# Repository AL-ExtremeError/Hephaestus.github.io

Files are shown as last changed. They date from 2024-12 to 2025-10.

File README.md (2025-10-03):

# Hephaestus.github.io

Welcome to the Hephaestus Build Guide!

<p align="center">
<a href="https://youtube.com/shorts/SWLXf19VgqY?feature=share" target="_blank">
  Youtube Video
</a>
</p>

****

For the updated **"Medusa"** build, please click here for that repository: https://github.com/AL-ExtremeError/Medusa

****

This guide will provide information, walk-thru's and files for a CoreXY Conversion of an Elegoo Neptune 4 Max 3d Printer in which I call, Hephaestus (heh-FESS-tus).

**Please Note:** Under the Build Documentation section, the links are listed in the order in which this build was done.

**Disclaimer:** This build is a DIY and at your own risk. There is no affiliation with Elegoo, Partners or vendors. I am not being compensated in my way for this. This walk-thru is strictly based on my own experience of my own personal challenge. I am not responsible for any mistakes, mis-interpretations and /or but not limited to mis-understandings. If something in this walk-thru is not clear or you would like to provide feedback (Good, Bad or Indifferent), please feel free reach out. I welcome all feedback and I am more than happy to answer / help walk-thru as best as I can.

**General Information**
* [Materials & Cost](https://github.com/AL-ExtremeError/Hephaestus.github.io/wiki/Hephaestus-Materials-&-Cost)
* [Design & Dimensions](https://github.com/AL-ExtremeError/Hephaestus.github.io/wiki/Hephaestus-Design-&-Dimensions)
* [Links](https://github.com/AL-ExtremeError/Hephaestus.github.io/wiki/Links)
* [Video Links](https://github.com/AL-ExtremeError/Hephaestus.github.io/wiki/Video-Links)

**Build Documentation**
* [Software Build](https://github.com/AL-ExtremeError/Hephaestus.github.io/wiki/Hephaestus-Build)
* [Cage Build](https://github.com/AL-ExtremeError/Hephaestus.github.io/wiki/Cage-Build)
* [Additional-Supports-&-Z-Axis-Build-Plate-Support](https://github.com/AL-ExtremeError/Hephaestus.github.io/wiki/Additional-Supports-&-Z-Axis-Build-Plate-Support)
* [Z-Axis Linear-Rails,-Stepper-Motors-&-Lead-Screws](https://github.com/AL-ExtremeError/Hephaestus.github.io/wiki/Z%E2%80%90Axis-%E2%80%90-Linear-Rails,-Stepper-Motors-&-Lead-Screws)
* [Bed Plate Build](https://github.com/AL-ExtremeError/Hephaestus.github.io/wiki/Bed-Plate-Build)
* [Y-Axis Build](https://github.com/AL-ExtremeError/Hephaestus.github.io/wiki/Y%E2%80%90Axis-Build)
* [X-Axis Build](https://github.com/AL-ExtremeError/Hephaestus.github.io/wiki/X%E2%80%90Axis-Build)
* [Stepper Motors, Belts & Tensioning](https://github.com/AL-ExtremeError/Hephaestus.github.io/wiki/Stepper-Motors,-Belts-&-Tensioning)
* [Print-Head-Tool-Mount](https://github.com/AL-ExtremeError/Hephaestus.github.io/wiki/Print-Head-%E2%80%90-Tool-Mount)
* [Board Box, Wiring & Electrical](https://github.com/AL-ExtremeError/Hephaestus.github.io/wiki/Board-Box,-Wiring-&-Electrical)
* [LED Light Bar](https://github.com/AL-ExtremeError/Hephaestus.github.io/wiki/LED-Light-Bar)

***

* **[Links](https://github.com/AL-ExtremeError/Hephaestus.github.io/wiki/Links)**

<p align="center">
<a href="https://ko-fi.com/alextremeerror" target="_blank">
  
</a>
</p>

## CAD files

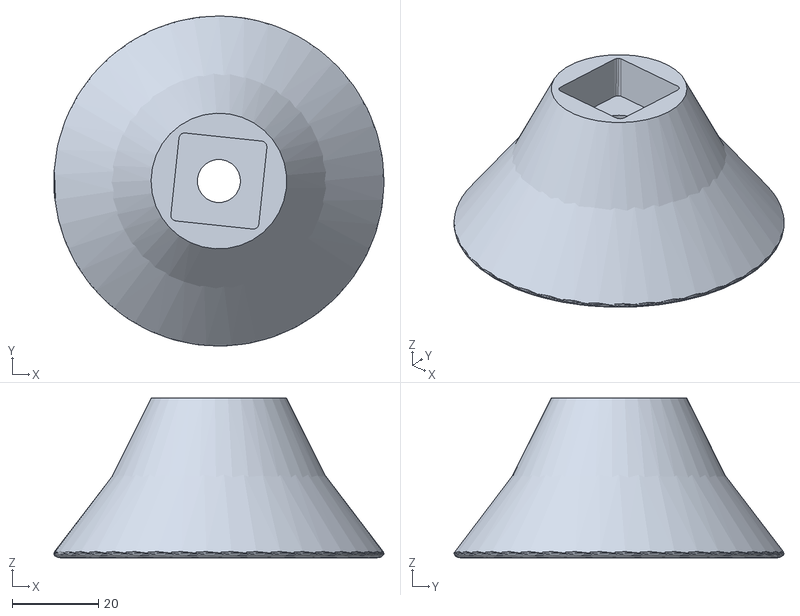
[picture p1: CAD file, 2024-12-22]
STL Files/Misc_Parts/Elegoo_Printer_Corner_Base_Feet.stl
76.5 x 76.5 x 37.0

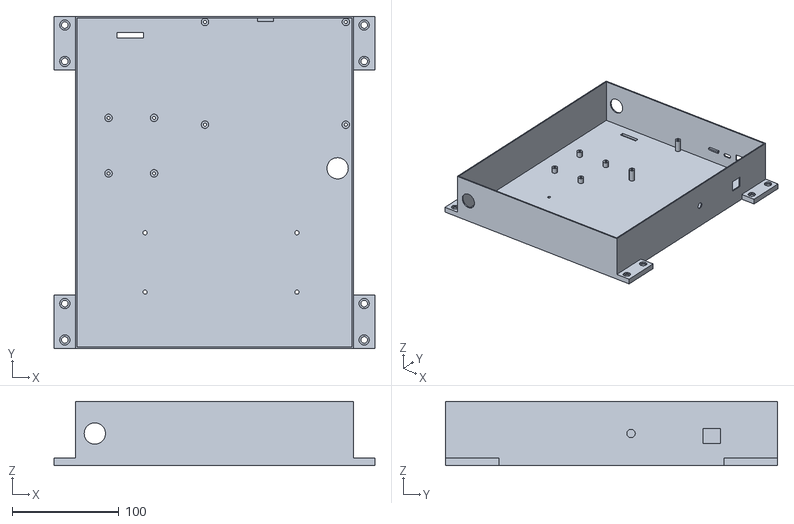
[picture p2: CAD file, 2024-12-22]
STL Files/PowerSupply and Board/Power_Supply_And_Board_Box.stl
300.0 x 310.5 x 60.0

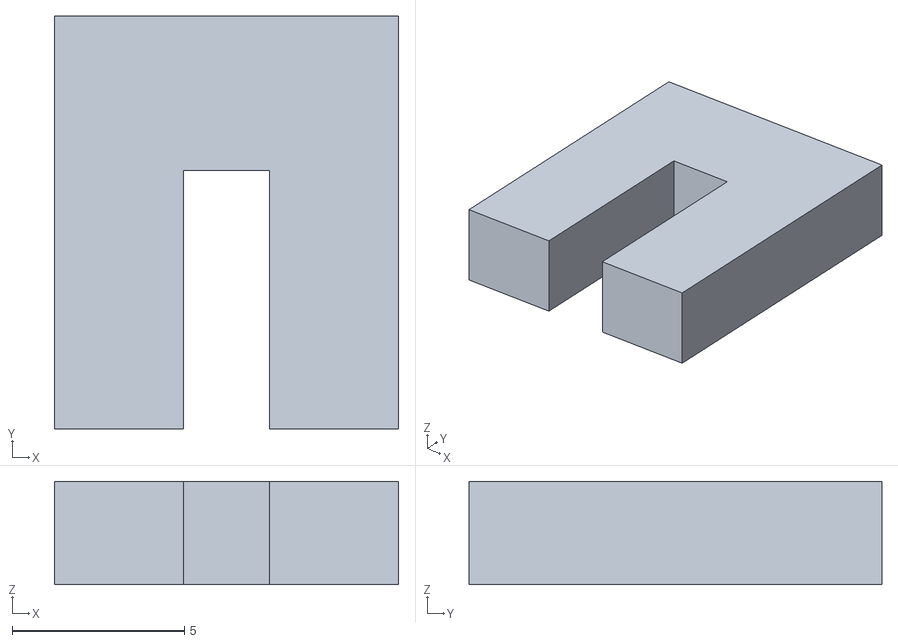
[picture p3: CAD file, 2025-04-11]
STL Files/X Axis Tool Head Carriage/X_Carriage_Belt_Clip_Shim.stl
10.0 x 12.0 x 3.00

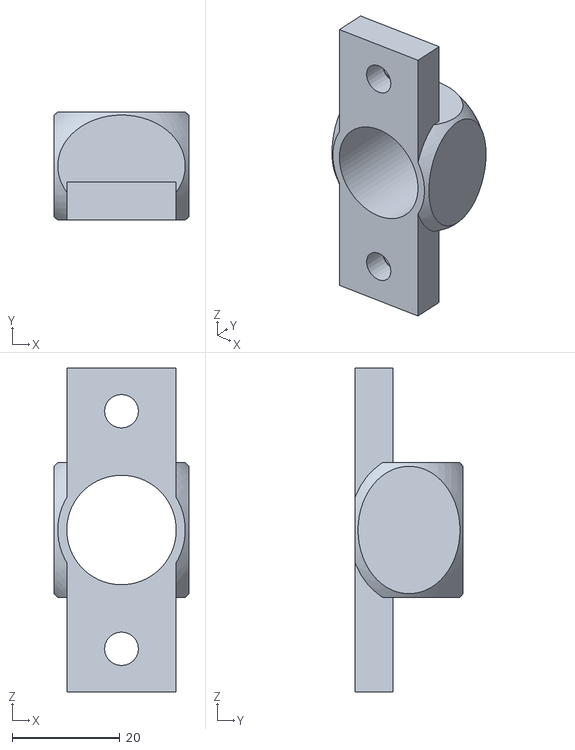
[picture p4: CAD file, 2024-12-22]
STL Files/Y Axis/Y_Axis_Rod_Holder_Front_V2_11.2.2024.stl
25.0 x 20.0 x 60.0

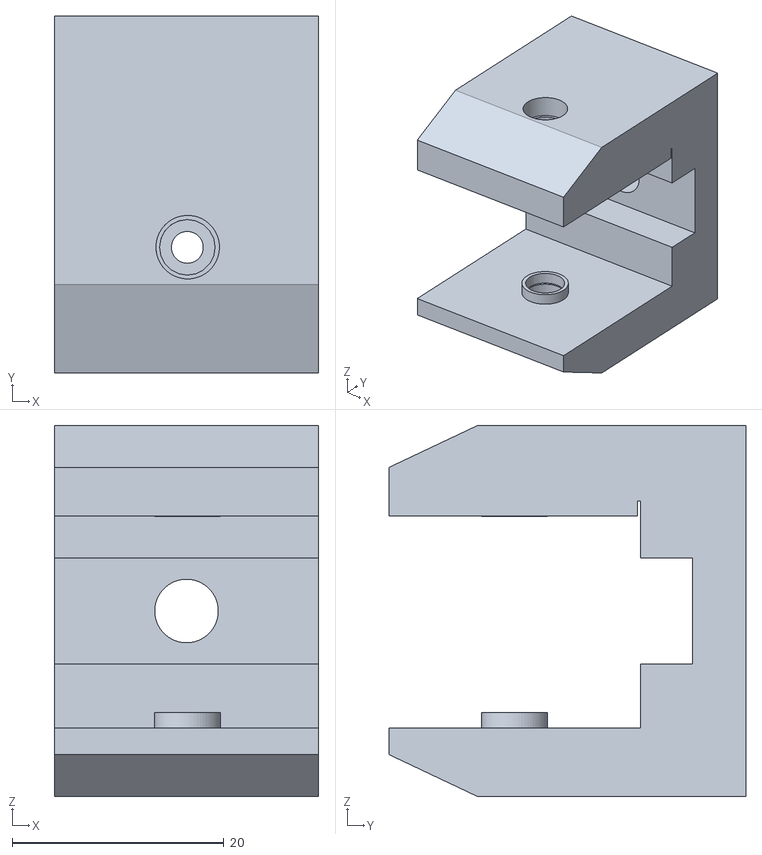
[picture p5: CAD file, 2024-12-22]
STL Files/Y Axis/Y_Pulley_Wheel_Holder/Y_Pulley_Wheel_Holder.stl
25.0 x 33.7 x 35.1

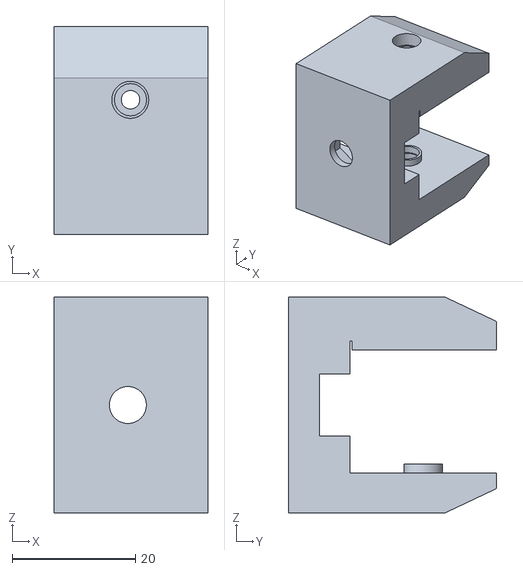
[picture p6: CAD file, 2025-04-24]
STL Files/Y Axis/Y_Pulley_Wheel_Holder_Alternate/Y_Pulley_Wheel_Holder_Alt.stl
25.0 x 33.7 x 35.1

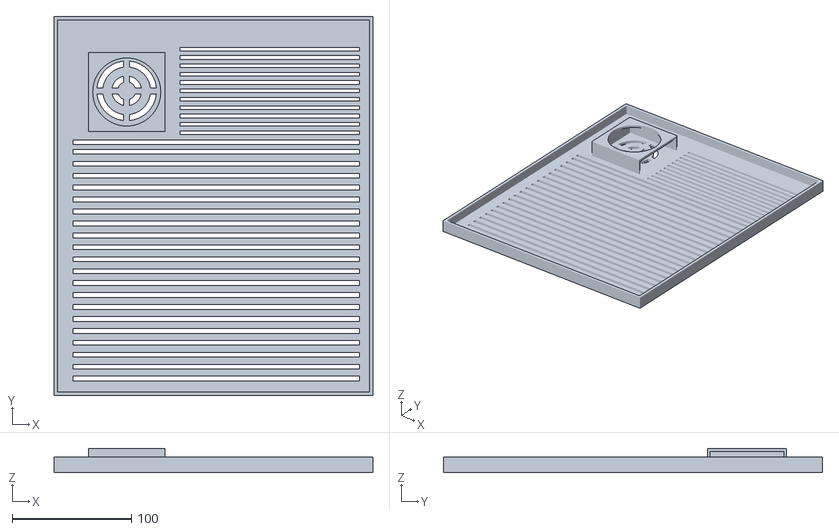
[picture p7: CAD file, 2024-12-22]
STL Files/PowerSupply and Board/Power_Supply_And_Board_Box_Cover.stl
267.0 x 317.5 x 20.3

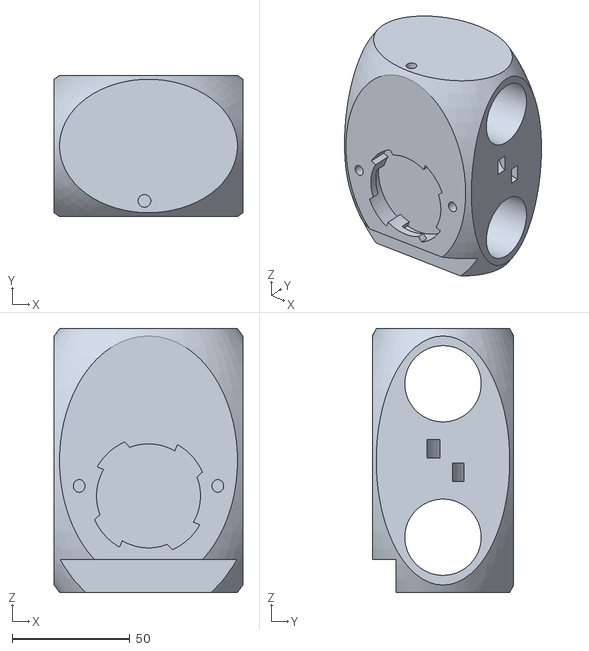
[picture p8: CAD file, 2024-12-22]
STL Files/X Axis Tool Head Carriage/X_Axis_Carriage_Tool_Carriage_V2_11.13.2024.stl
80.0 x 60.0 x 112.0

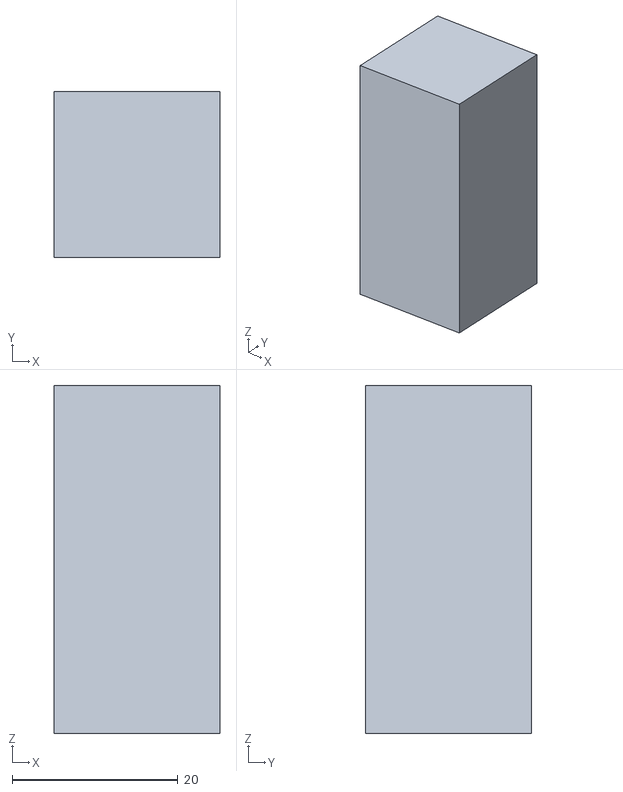
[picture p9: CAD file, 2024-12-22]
STL Files/Y Axis/Y_Axis_Rod_Setting_Bar.2024.stl
20.0 x 20.0 x 42.0

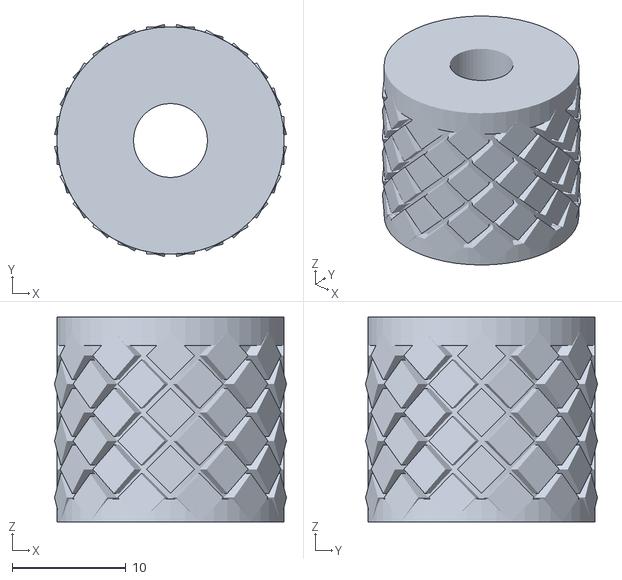
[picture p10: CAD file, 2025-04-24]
STL Files/Y Axis/Y_Pulley_Wheel_Holder_Alternate/Y_Pulley_Wheel_Holder_Alt_Knob.stl
20.4 x 20.4 x 18.0

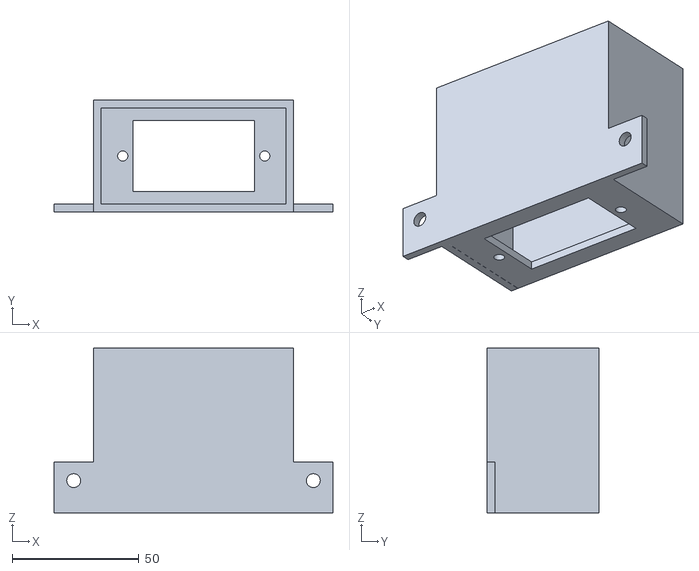
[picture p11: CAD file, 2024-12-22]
STL Files/PowerSupply and Board/Power_Supply_Switch_Box.stl
110.0 x 44.0 x 65.0

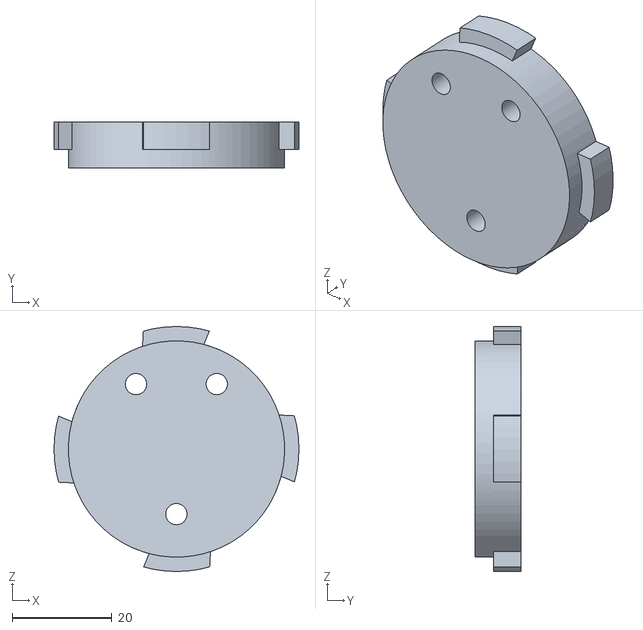
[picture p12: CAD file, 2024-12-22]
STL Files/X Axis Tool Head Carriage/X_Axis_Carriage_Tool_Mount_V2_11.3.2024.stl
49.0 x 9.25 x 49.0

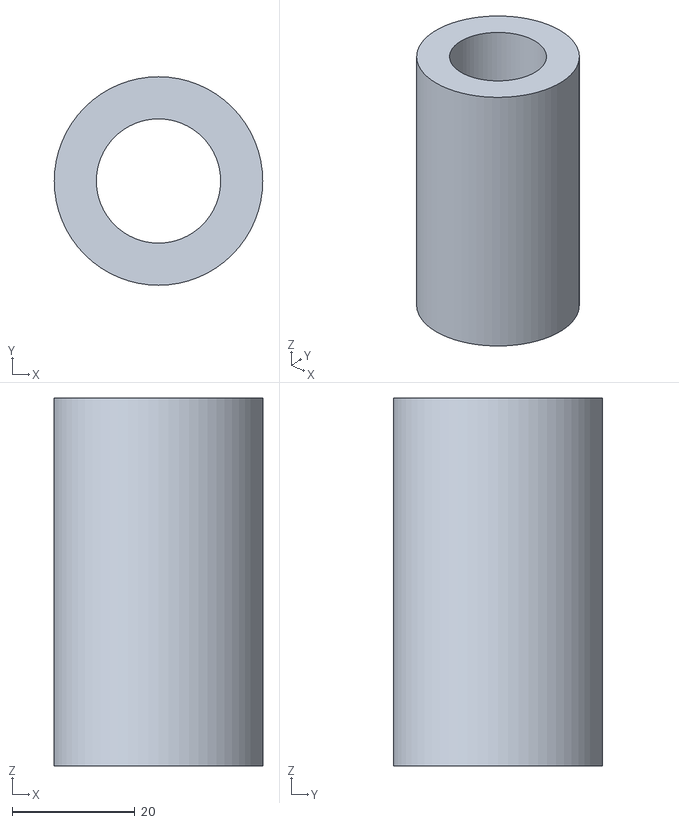
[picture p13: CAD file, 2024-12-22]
STL Files/Y Axis/End_Stops_Front_11.13.2024.stl
34.0 x 34.0 x 60.0

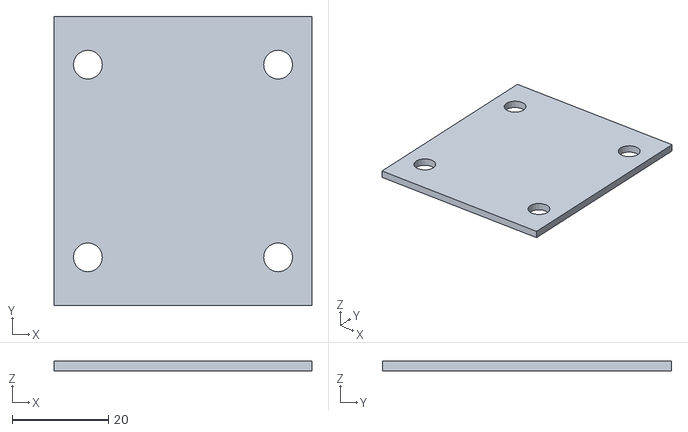
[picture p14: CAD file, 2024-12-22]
STL Files/Z Axis/Z Axis_Carriage_Shim.stl
53.5 x 60.0 x 2.00

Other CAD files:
STL Files/Y Axis/Y_Axis_Carriage_V3_11.24.2024.stl
STL Files/Y Axis/Y_Pulley_Tensioner_Rear_Right.stl
STL Files/Y Axis/Y_Axis_Rod_Holder_Rear_Left_V3_11.13.2024.stl
STL Files/Z Axis/Z_Axis_Nut_Block.stl
STL Files/Z Axis/Z_Axis_Nut_Block_Spacer.stl

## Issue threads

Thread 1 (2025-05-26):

Firmware version for two Z motors from one driver

DBSDBS, 2025-05-26:
Hello,

Is there a version for the firmware that uses the original configuration with single driver for the two Z motors?

Thank you in advance.

Denis

AL-ExtremeError, 2025-05-26:
If you mean to control the two motors individually, no. Not that I am aware of anyway.

The driver supports one channel for lack of a better term. So whatever signal is sent from that "channel" is what will be received by whatever is connected to it.

If you want to control each motor individually, then each one will need a driver independently.

Now if you jist want to connect two Z motors to have them driven by one driver, the neptune 4 max is already setup that way from stock as it uses a splitter cable to connect both stepper motors to one driver. Unfortunately, this means that that is no independency but will suffice to get z moving with 2 motors.

I hope this helps

DBSDBS, 2025-05-26:
Thank you for the replay...
Because you share a CoreXY firmware that is modified also for two drivers (Z and E1) to drive separately the two Z motors (in yours case), I asked for the same firmware made from you for CoreXY but without Z section modifications - only original one driver for Z.

DBSDBS, 2025-05-27:
I'm using opennep4tune firmware. What should I to exchange in it to be able to use your version of CoreXY N4M?

AL-ExtremeError, 2025-06-06:
I am so sorry, I never got an alert that you had replied. The default items within the printer.cfg file that come with opennep4tune should work fine as I was using the default when I did it. The only thing is you will need to make sure your gpio's are configured correctly and small details like that but over all it should all work with default.

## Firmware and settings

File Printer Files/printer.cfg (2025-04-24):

#----------------------------------------------------------------------------
#      ____                _  __         __  ____              
#     / __ \___  ___ ___  / |/ /__ ___  / /_/ / /__ _____  ___ 
#    / /_/ / _ \/ -_) _ \/    / -_) _ \/ __/_  _/ // / _ \/ -_)
#    \____/ .__/\__/_//_/_/|_/\__/ .__/\__/ /_/ \_,_/_//_/\__/ 
#        /_/                    /_/                            
#----------------------------------------------------------------------------
;   Neptune 4 Series Custom Image by (OpenNeptune3D/OpenNept4une):
#----------------------------------------------------------------------------
; Wiki    : https://github.com/OpenNeptune3D/OpenNept4une/wiki
; Discord : https://discord.com/invite/X6kwchT6WM

#############################################################################
#   External Config Includes
#############################################################################
[include mainsail.cfg]          ; mainsail runs on port 81 (http://IP_ADDRESS:81)
[include fluidd.cfg]
[include KAMP_Settings.cfg]
[include Adaptive_Meshing.cfg] 
[include Smart_Park.cfg]
[include Line_Purge.cfg]
#[include shell_command.cfg]
#[include klipper_debug.cfg]
#[include adxl.cfg]             ; Comment this out when you disconnect the Pico/MellowFly
#[include timelapse.cfg]


#############################################################################
#   Base Config
#############################################################################

[virtual_sdcard]
path: ~/printer_data/gcodes
[display_status]
[pause_resume]

[mcu]
serial: /dev/ttyS0 ; The hardware use USART1 PA10/PA9 connect to RK3328
baud: 250000
restart_method: command

[printer]
kinematics: corexy
max_velocity: 500
max_accel: 10000
max_z_velocity: 8
max_z_accel: 120
square_corner_velocity: 9.0
minimum_cruise_ratio: 0.1

[respond]
[gcode_arcs]
[pause_resume]
[display_status]
[exclude_object]
[firmware_retraction]
[virtual_sdcard]
path: ~/printer_data/gcodes
[force_move]
enable_force_move : True
[idle_timeout]
timeout: 2100                  ; 35min idle timeout (when not paused or printing)

#############################################################################
#   X/Y/Z Stepper Config
#############################################################################

[stepper_x]
step_pin: PC14
dir_pin: PC13
enable_pin: !PC15
microsteps: 64
rotation_distance: 40
full_steps_per_rotation:200                  ; set to 400 for 0.9 degree stepper
endstop_pin: tmc2209_stepper_x:virtual_endstop
position_min: 0
position_max: 415
position_endstop: 415
homing_speed: 40
homing_retract_dist: 0
homing_positive_dir: True

[stepper_y]
step_pin: PB4
dir_pin: !PB3
enable_pin: !PC15
microsteps: 64
rotation_distance: 40
full_steps_per_rotation:200                  ; set to 400 for 0.9 degree stepper
endstop_pin: tmc2209_stepper_y:virtual_endstop
position_min: 0
position_max: 415
position_endstop: 415
homing_speed:40
homing_retract_dist: 0
homing_positive_dir: True

[stepper_z]
step_pin: PC10
dir_pin: PA13
enable_pin: !PC11
microsteps: 32
rotation_distance: 2
full_steps_per_rotation: 200
endstop_pin:probe:z_virtual_endstop
position_min: -1
position_max: 700
homing_speed: 8
second_homing_speed: 3
homing_retract_dist: 5
homing_positive_dir: False


[stepper_z1]
step_pin: PB1
dir_pin: !PB2
enable_pin: !PB0
microsteps: 32
rotation_distance: 2
full_steps_per_rotation: 200
endstop_pin:probe:z_virtual_endstop




#############################################################################
#   TMC Stepper-driver UART Config
#############################################################################

[tmc2209 stepper_x]
uart_pin: PB9
run_current: 1.0
interpolate: True
stealthchop_threshold: 0
driver_SGTHRS: 70
diag_pin: ^PC0

[tmc2209 stepper_y]
uart_pin: PD2
run_current: 1.4
interpolate: True
stealthchop_threshold: 0
driver_SGTHRS: 70
diag_pin: ^PB8

[tmc2209 stepper_z]
uart_pin: PC5
run_current: 0.8
#hold_current: 0.5
interpolate: True
stealthchop_threshold: 0
driver_SGTHRS: 200

[tmc2209 stepper_z1]
uart_pin: PB6
run_current: 0.8
hold_current: 0.5
interpolate: True
stealthchop_threshold: 0
driver_SGTHRS: 200

[tmc2209 extruder]
uart_pin: PC4
run_current: 0.7
hold_current: 0.5
interpolate: True
stealthchop_threshold: 0

[z_tilt]
z_positions:
    30,180   # X, Y position of the first Z motor
    410,180  # X, Y position of the second Z motor
points:
    30,180   # X, Y position of the first Z motor
    410,180  # X, Y position of the second Z motor
speed: 50
horizontal_move_z: 5
retries: 25
retry_tolerance: 0.001



#############################################################################
#   Probe Config
#############################################################################

[probe]
pin:^PA11
x_offset: -20
y_offset: 20.45
#z_offset = 0.0
speed: 10.0
samples: 7
samples_result: median 
sample_retract_dist: 3.0
samples_tolerance: 0.025
samples_tolerance_retries: 3

[bed_mesh]
speed:300                
horizontal_move_z:5  
mesh_min: 10,21
mesh_max: 400,404
probe_count: 11,11          
algorithm:bicubic
bicubic_tension:0.2
mesh_pps: 4, 4 
fade_start: 0 ;Old setting 1.0
fade_end: 10.0 

#############################################################################
#   Print Start & End Macros
#############################################################################

[gcode_macro PRINT_START]   
gcode:
    SET_FILAMENT_SENSOR SENSOR=filament_sensor ENABLE=1
    G92 E0 
    G90                       ; Use absolute coordinates
    M117 Clear Bed Mesh
    BED_MESH_CLEAR    
       
    {% set BED_TEMP = params.BED_TEMP|default(60)|float %}
    {% set BED_HEAT_SOAK_MINUTES = params.BED_HEAT_SOAK_MINUTES|default(0)|float %}
    {% set BED_MESH = params.BED_MESH|default('adaptive')|string %} ; One of: adaptive (default), full, default (or any other value as the bed mesh profile name), none
    {% set EXTRUDER_TEMP = params.EXTRUDER_TEMP|default(200)|float %}


    SET_BED_TEMPERATURE TARGET={BED_TEMP}                           ; Heat Bed to target temp
    BED_TEMPERATURE_WAIT MINIMUM={BED_TEMP-2} MAXIMUM={BED_TEMP+4}  ; Waits until the bed reaches close to target
    {% if BED_HEAT_SOAK_MINUTES > 0 %}
    RESPOND MSG="Waiting {BED_HEAT_SOAK_MINUTES} minutes for the bed to settle."
    G4 P{BED_HEAT_SOAK_MINUTES * 60000}
    {% endif %}

    CG28
    
    M117 Prep Bed Mesh
    {% if BED_MESH == 'full' %}
    BED_MESH_CALIBRATE
    {% elif BED_MESH == 'adaptive' %}
    BED_MESH_CALIBRATE ADAPTIVE=1
    {% elif BED_MESH != 'none' %}
    BED_MESH_PROFILE LOAD={BED_MESH}
    {% endif %}
    #SET_FILAMENT_SENSOR SENSOR=filament_sensor ENABLE=1
    SET_HEATER_TEMPERATURE HEATER=extruder TARGET={EXTRUDER_TEMP}   ; Set and heat the final extruder temperature
    TEMPERATURE_WAIT SENSOR=extruder MINIMUM={EXTRUDER_TEMP-4} MAXIMUM={EXTRUDER_TEMP+10}  ; Wait for extruder to reach near target temperature

    M117 Printing
    G92 E0                                                          ; Reset Extruder
    G1 Z2.0 F3000                                                   ; Move Z Axis up 
    #KAMP Smart Park
    SMART_PARK
    #KAMP Line Purge
    LINE_PURGE                                                      ; KAMP Line Purge near print
              
       
[gcode_macro PRINT_END]
gcode:
    M117 Completed
    M400                    ; wait for buffer to clear
    TURN_OFF_HEATERS
    G92 E0                  ; zero the extruder
    G91                     ; Relative positioning
    G1 E-2 F2700            ; Retract a bit
    G1 X5 Y5 F3000          ; Wipe out
    G1 E-2 Z0.2 F1600       ; Retract and raise Z
    G1 Z4 F3000             ; Raise Z more
    G90                     ; Absolute positioning
    G1 X415 Y415            ; Present print
    END_TUNE                ; Print End Beeper Jingle
    M107                    ; turn off fan
    M84                     ; turn off steppers
    SET_FILAMENT_SENSOR SENSOR=filament_sensor ENABLE=1


#############################################################################
#   Pause, Resume & Cancel Macros
#############################################################################
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

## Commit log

2024-12-22 Add files via upload
    This file can be found on Printables.com: https://www.printables.com/model/1117834-2020-ninjaflex-foot-slightly-taller
    37mm in height. Does not take into account the depth of the aluminum extrusion insertion.
    This was a remix of : https://www.printables.com/model/192682-2020-aluminum-extrusion-foot
    [Elegoo_Printer_Corner_Base_Feet.stl]
2024-12-22 Corner Base Feet
    [Elegoo_Printer_Corner_Base_Feet.stl]
2024-12-22 STL Files
    [End_Stops_Front_11.13.2024.stl, Power_Supply_And_Board_Box.stl, Power_Supply_And_Board_Box_Cover.stl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]
2025-04-24 Rename printer.cfg to Printer Files/printer.cfg
    [printer.cfg]
2025-04-24 Rename STL Files/Y Axis/Y_Pulley_Wheel_Holder.stl to STL Files/Y Axis/Y_Pulley_Wheel_Holder/Y_Pulley_Wheel_Holder.stl
    [Y_Pulley_Wheel_Holder.stl]
2025-04-24 Alternate Pulley Wheel Holder & Knob
    This is an alternate version using an M5 x 30mm Hex Head Bolt and an M5 Heated Insert for the knob. Alternate design by @chaosstar68 on reddit : https://www.reddit.com/user/chaosstar68/
    [Y_Pulley_Wheel_Holder_Alt.stl, Y_Pulley_Wheel_Holder_Alt_Knob.stl]
2025-04-24 Rename STL Files/Y Axis/Y_Pulley_Wheel_Holder/Y_Pulley_Wheel_Holder.stl to STL Files/Y Axis/Y_Pulley_Wheel_Holder.stl
    [Y_Pulley_Wheel_Holder.stl]
